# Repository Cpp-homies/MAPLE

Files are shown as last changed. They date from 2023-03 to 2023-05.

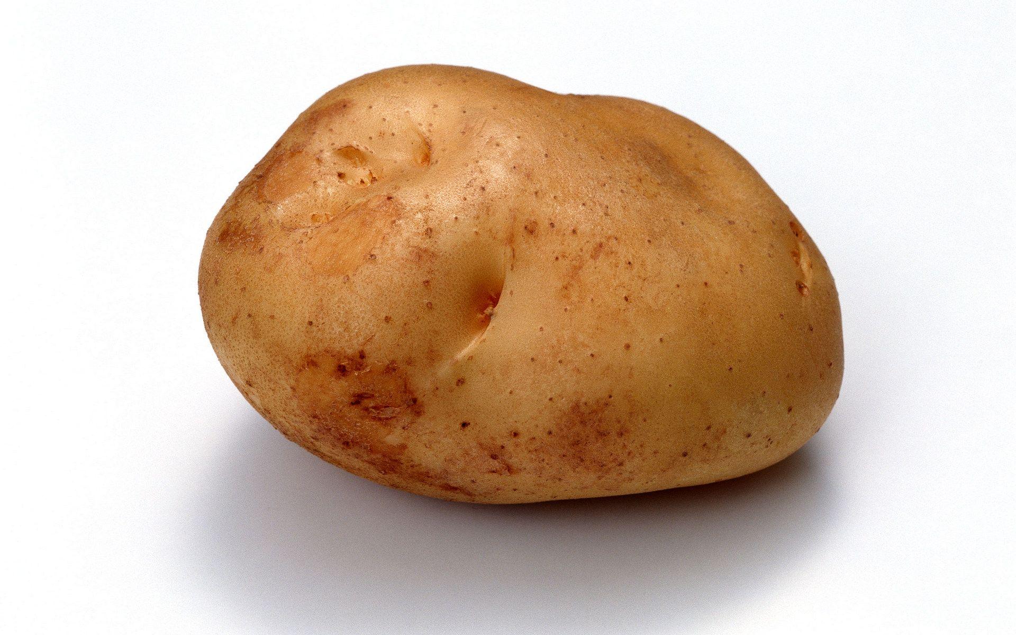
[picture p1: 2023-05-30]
Cloud/images_/potato.jpeg

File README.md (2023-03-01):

# M.A.P.L.E: Modular Automated Plant Life Enclosure

## Introduction to the project
Welcome to the public repository for our Design Thinking and Advanced Prototyping (ELEC-C9821) project, completed during the spring of 2023. Here, you can track the progress of our product development and review the process we followed to arrive at our final solution.

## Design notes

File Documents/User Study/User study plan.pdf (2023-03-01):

# User study plan - Team 3

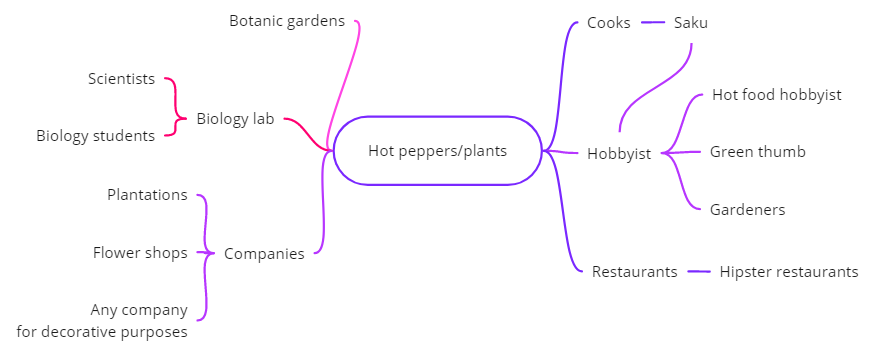
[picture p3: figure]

## 1. Target users

Since the trackable resource that we are interested in is plants, we have chosen hobbyists and enthusiasts as our target users, as they are potentially in need of plant-care automation. These users are also directly related to the resource (plants/hot peppers) since they are likely to have plants under their care.

This user group is quite accessible, as they could theoretically be anyone. For instance, we can reach out to other students in Aalto or other Universities and ask them to participate in our user study.

## 2. Methods

We have chosen to use multiple methods. To get a general understanding of peoples’ needs, we are conducting online surveys that are shared in facebook groups and also forwarded to enthusiasts and students by friends and family. The surveys are accessible through these links:

1. (Finnish)

https://docs.google.com/forms/d/e/1FAIpQLSeV6fbw9r-klXWt46JdWvNCtC_DFmbpAS877YtbKPnmx8KQeA/viewform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 (https://docs.google.com/forms/d/e/1FAIpQLSeV6fbw9r-klXWt46JdWvNCtC_DFmbpAS877YtbKPnmx8KQeA/viewform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)

2. (English)
https://docs.google.com/forms/d/e/1FAIpQLSdVMB6B2ZC3AZEyyUIAWT1qNiN2gCB68X5xvfQQSQ_5HiJimA/viewform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 (https://docs.google.com/forms/d/e/1FAIpQLSdVMB6B2ZC3AZEyyUIAWT1qNiN2gCB68X5xvfQQSQ_5HiJimA/viewform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)

Other methods of user studies will involve in-person or remote interviews mixed with co-design and design probing methods, if possible. That would give us a more personal view to the daily activities of enthusiasts and would open up the possibility for future user testing. (The first interview has already been arranged)

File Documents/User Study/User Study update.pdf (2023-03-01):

# User Study Update - Team 3

## 1. Target users

Our target users are plant hobbyists and enthusiasts. They are much more inclined to monitor their plants to a higher degree, and thus would be interested in a device to automate the monitoring of their plants to some extent.

This user group is quite accessible, as they could theoretically be anyone. For instance, we can reach out to other students in Aalto or other Universities and ask them to participate in our user study.

## 2. Current situation

We have already gotten 39 rather thorough responses with the online surveys that have given us a good insight into what people might be looking for in an IoT device meant for plant cultivation. In addition, the first interview has already been conducted and documented. It was a group interview with 2 potential users and was really informative. We believe the fact that 2 users could bounce ideas off of each other made it much more informative for us than it would have been otherwise.
Since we have already gathered enough information, we have started to map out the features and components of the device to slowly narrow down the idea.

Link to survey responses (english version): https://docs.google.com/spreadsheets/d/17iAOfix5XNTlHRVkv8-SSzz-9DiBaFzHnPxrE1_Iep0/edit?usp=sharing (https://docs.google.com/spreadsheets/d/17iAOfix5XNTlHRVkv8-SSzz-9DiBaFzHnPxrE1_Iep0/edit?usp=sharing)
Link to survey responses (finnish version): https://docs.google.com/spreadsheets/d/10vmuCnAydOV0NJCwSoHKujVEs_3GuGNUji77kcqlbv0/edit?usp=sharing (https://docs.google.com/spreadsheets/d/10vmuCnAydOV0NJCwSoHKujVEs_3GuGNUji77kcqlbv0/edit?usp=sharing)
Link to first interview notes: https://docs.google.com/document/d/13SDdg8U_1lrDhgf8Mg7o01ts4Be4uMcnlehz204QAec/edit?usp=sharing (https://docs.google.com/document/d/13SDdg8U_1lrDhgf8Mg7o01ts4Be4uMcnlehz204QAec/edit?usp=sharing)
Link to team Miro board:
https://miro.com/app/board/uXjVPy4PPEA=/?share_link_id=984503807965

## 3. User study methods

We have chosen to use multiple methods. To get a general understanding of people’s needs, we are conducting online surveys that are shared in facebook groups and also forwarded to enthusiasts and students by friends and family.

Other methods of user studies will involve in-person or remote interviews mixed with co-design and design probing methods, if possible. That would give us a more personal view of the daily activities of enthusiasts and would open up the possibility for future user testing.

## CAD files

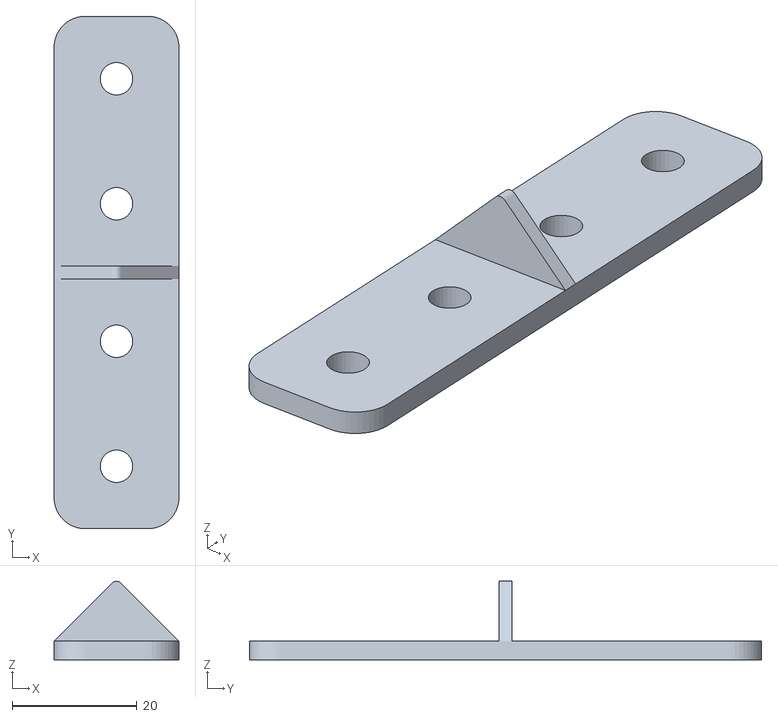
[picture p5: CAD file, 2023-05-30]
Physical/Frame/VerticalJoint.stl
20.0 x 82.0 x 12.6

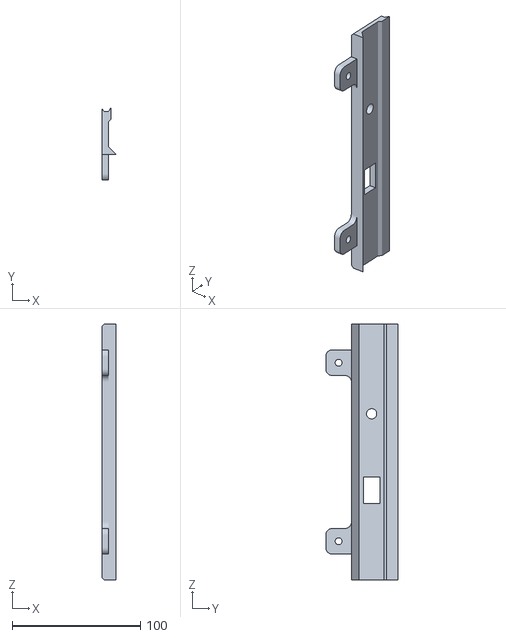
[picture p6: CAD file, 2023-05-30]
Physical/Panel/PanelHolder-Power v1.stl
11.2 x 56.5 x 199.6

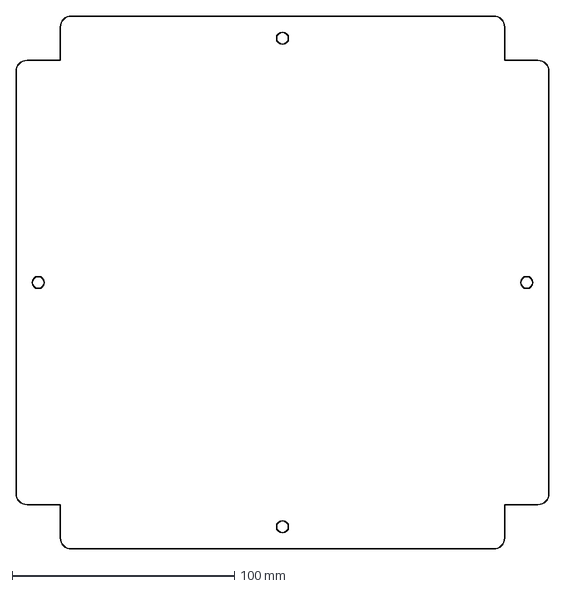
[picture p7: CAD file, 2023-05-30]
Physical/Plates/TopPanel v2.dxf
240.0 x 240.0 mm

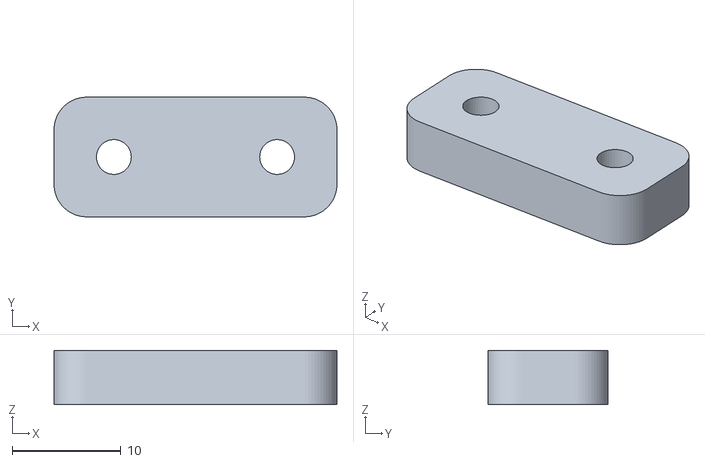
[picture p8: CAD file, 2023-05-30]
Physical/Pump/EndClamp v1.stl
26.0 x 11.0 x 5.00

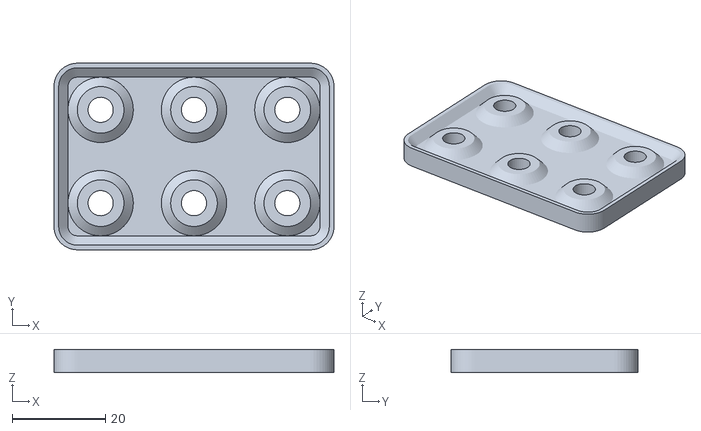
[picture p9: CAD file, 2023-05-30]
Physical/Frame/TBaseJoint v1.stl
60.0 x 40.0 x 5.00

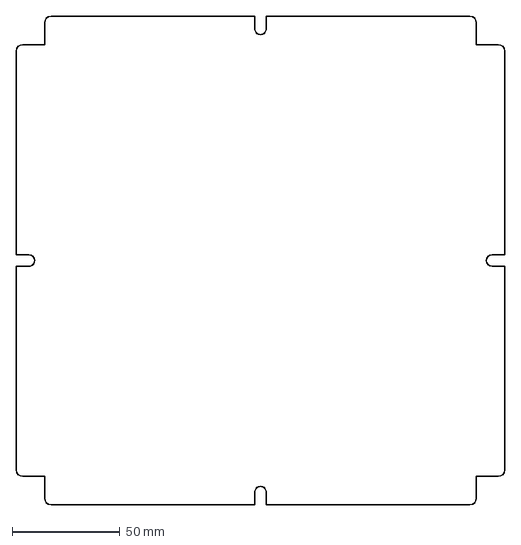
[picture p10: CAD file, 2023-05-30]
Physical/Plates/BottomPanel v1.dxf
226.0 x 226.0 mm

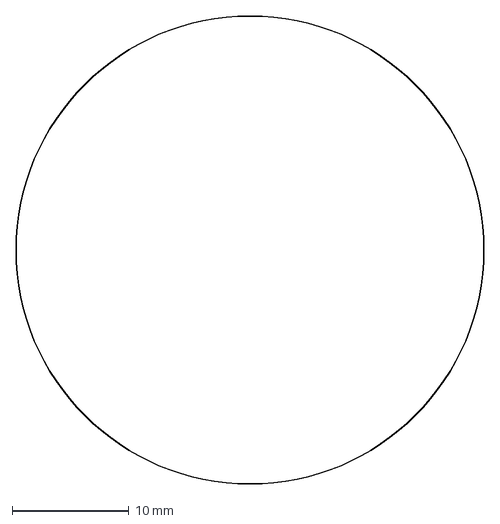
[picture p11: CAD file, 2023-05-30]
Physical/Plates/FanHole.dxf
40.0 x 40.0 mm

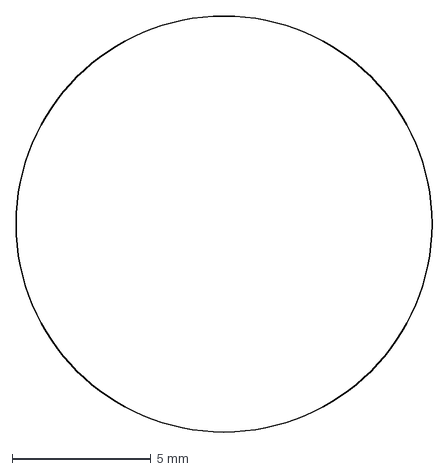
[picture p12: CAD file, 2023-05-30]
Physical/Plates/CableHole.dxf
15.0 x 15.0 mm

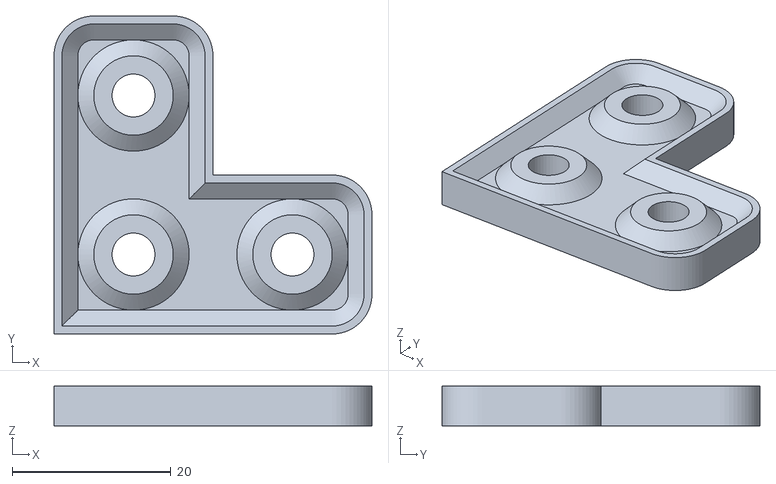
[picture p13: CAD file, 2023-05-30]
Physical/Frame/CornerJoint v2.stl
40.0 x 40.0 x 5.00

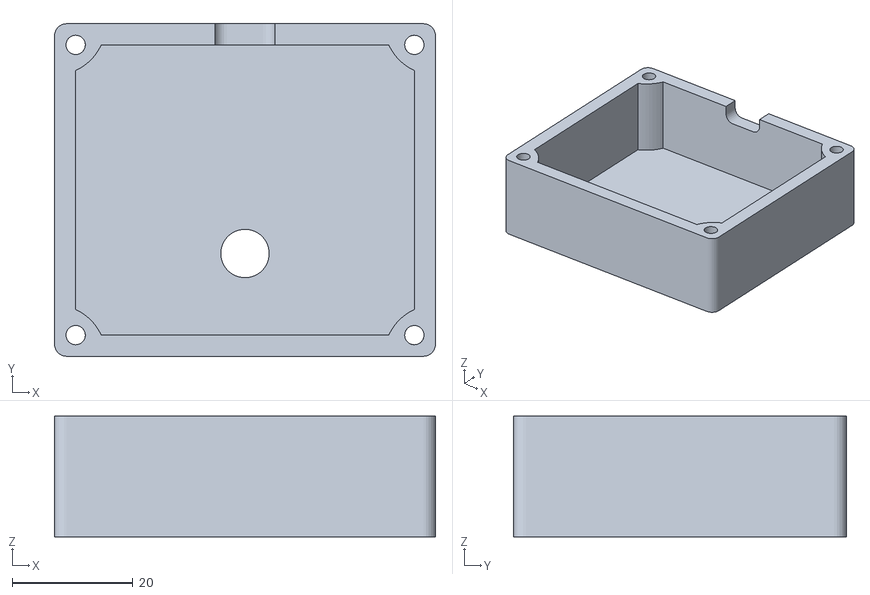
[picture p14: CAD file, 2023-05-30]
Physical/Mounts/ControlHolderC v2.stl
63.0 x 55.0 x 20.0

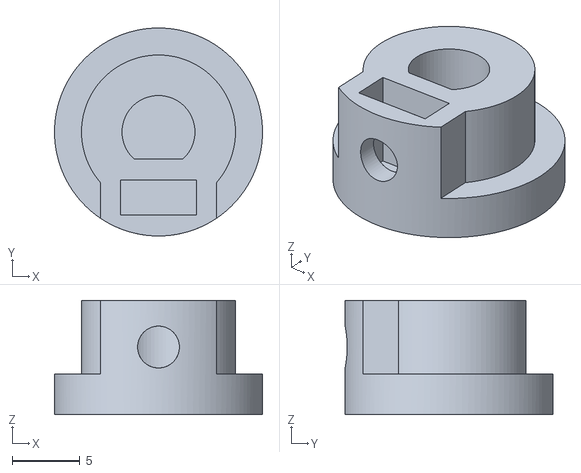
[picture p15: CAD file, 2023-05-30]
Physical/Pump/Stopper v2.stl
15.4 x 15.4 x 8.45

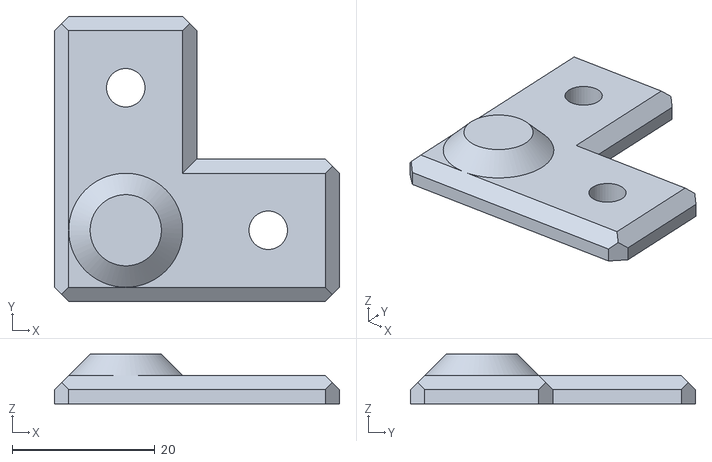
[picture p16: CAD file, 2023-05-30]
Physical/Frame/Feet v2.stl
40.0 x 40.0 x 7.00

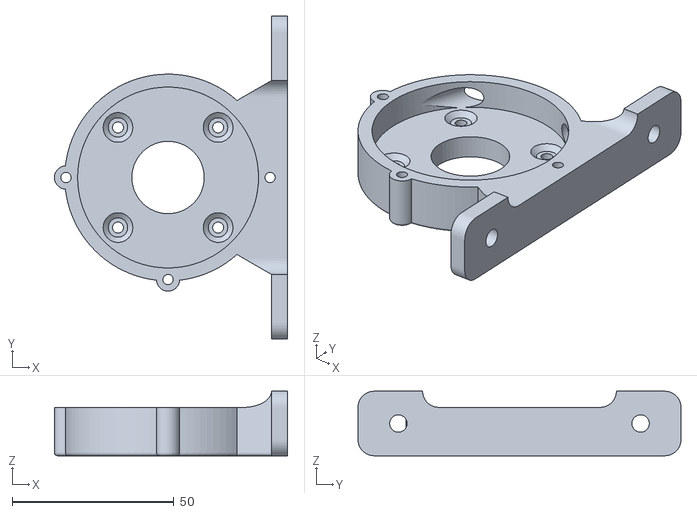
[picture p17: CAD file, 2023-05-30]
Physical/Pump/Pump v5.stl
72.2 x 100.0 x 20.0

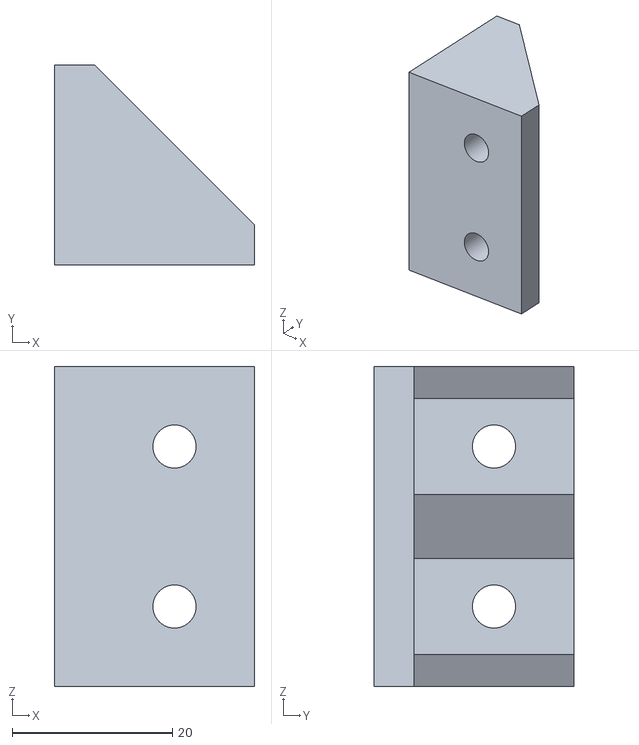
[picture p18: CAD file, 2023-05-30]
Physical/Frame/InternalJoint40 v1.stl
25.0 x 25.0 x 40.0

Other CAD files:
Physical/Panel/PanelHolder-Tube v1.stl
Physical/Mounts/ControllerBox v2.stl
Physical/Panel/Gripper v1.stl
Physical/Frame/CornerJoint.stl
Physical/Frame/CableCorner v1.stl
Physical/Frame/CableCorner v2.stl
Physical/Frame/CornerJointB v1.stl
Physical/Frame/Feet v1.stl
Physical/Frame/InternalJoint20 v1.stl
Physical/Frame/TTopJoint v1.stl
Physical/Frame/VerticalJoint v2.stl
Physical/Frame/VerticalJoint v3.stl
Physical/Frame/VerticalJoint v4.stl
Physical/Mounts/CableHolder v1.stl
Physical/Mounts/CableHolder v2.stl
Physical/Mounts/CableHolder v3.stl
Physical/Mounts/CableHolder-Flat v1.stl
Physical/Mounts/CableHolder-Flat v2.stl
Physical/Mounts/CameraMount v1.stl
Physical/Mounts/CameraMount v2.stl
Physical/Mounts/CameraMount v3.stl
Physical/Mounts/CameraMountB v1.stl
Physical/Mounts/CameraMountB v2.stl
Physical/Mounts/ConnectorMount v1.stl
Physical/Mounts/ConnectorMountL v1.stl
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

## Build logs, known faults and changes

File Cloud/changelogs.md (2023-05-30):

## Change logs
### — Recent changes —
### 24/05
**App to Cloud interaction**

- Data in a given time range can be requested through "/get-range/\<string:user_id\>/\<string:timerange\>"
    The format of the timerange is "%Y_%m_%d_%H_%M_%S-%Y_%m_%d_%H_%M_%S", or in other words, two time instances with start and end separated by the hyphen '-' character. 

    It is also possible to use the shorthand 'now' in place of the end time, which will result in a string with the form "%Y_%m_%d_%H_%M_%S-now". This will query data from the start time until the current time.
    
### 05/05
**App to Cloud interaction**  

- New method for deleting all data rows associated with a user was added. After authentication this can be accessed at "\<baseurl\>/delete-all/\<string:user_id\>"

### — Archived changes — 
### 11/04
**Device to Cloud interaction**

- The "\<baseurl\>/request-to-esp/\<user_id:string\>" is now moved to "\<baseurl\>/request-to-esp/\<user_id:string\>/\<password:string\>"
- A new URL was made specifically for PUT request from the ESP, at "\<baseurl\>/esp-req/sensordata/&lt;string:timestamp&gt;" with the "user_id" and "password" being added to the arguments

### 07/04
**App to Cloud interaction**

- A new user_id and password hash pair can be add to the database by sending PUT to "\<base url\>/auth/register" with two parameters "user_id" and "password"
- A hashed user_id and password pair can be check by sending GET to "\<base url\>/auth/login" with two parameters "user_id" and "password". This will have the following return values
	- 404 HTTP response code: username not found
	- a dictionary with "status" attributes:
		- `response["status"] == 0`: password does not match the one in the database, authentication failed
		- `response["status"] == 1`: password matches the one in the database, authentication was successful
- User's password can be change using PATCH requets to "\<base url\>/auth/login" with two parameters "user_id" and "password".
- A session must be authenticate by logging in first before any request can be made.
- 

### 05/04
**App to Cloud interaction**

- For PUT and UPDATE request: added soil humidity "soil_humid", the old "humid" key in the json will be change to "air_humid"
- For GET request: added soil humidity "soil_humidity", and change the old "humid" key into "air_humidity"
- Sensor data resource now located at "\<base url\>/sensordata/\<string:user_id\>/\<string:timestamp\>" instead of "\<base url\>/sensordata/\<string:timestamp\>/" in order to distinguish data entries from different users and their devices. All requests that previously went to the mentioned URL should now be redirected to the new one.
- The "\<baseurl\>/datatable" resource is now moved to "\<baseurl\>/datatable/\<user_id:string\>" to distinguish between the users. All requests that previously went to the mentioned URL should now be redirected to the new one.

**Device to Cloud interaction**

- The "\<baseurl\>/datatable" resource is now moved to "\<baseurl\>/datatable/\<user_id:string\>" to distinguish between the users
- The "\<baseurl\>/request-to-esp" resource is now moved to "\<baseurl\>/request-to-esp/\<user_id:string\>" to distinguish between the users. All requests that previously went to the mentioned URL should now be redirected to the new one.

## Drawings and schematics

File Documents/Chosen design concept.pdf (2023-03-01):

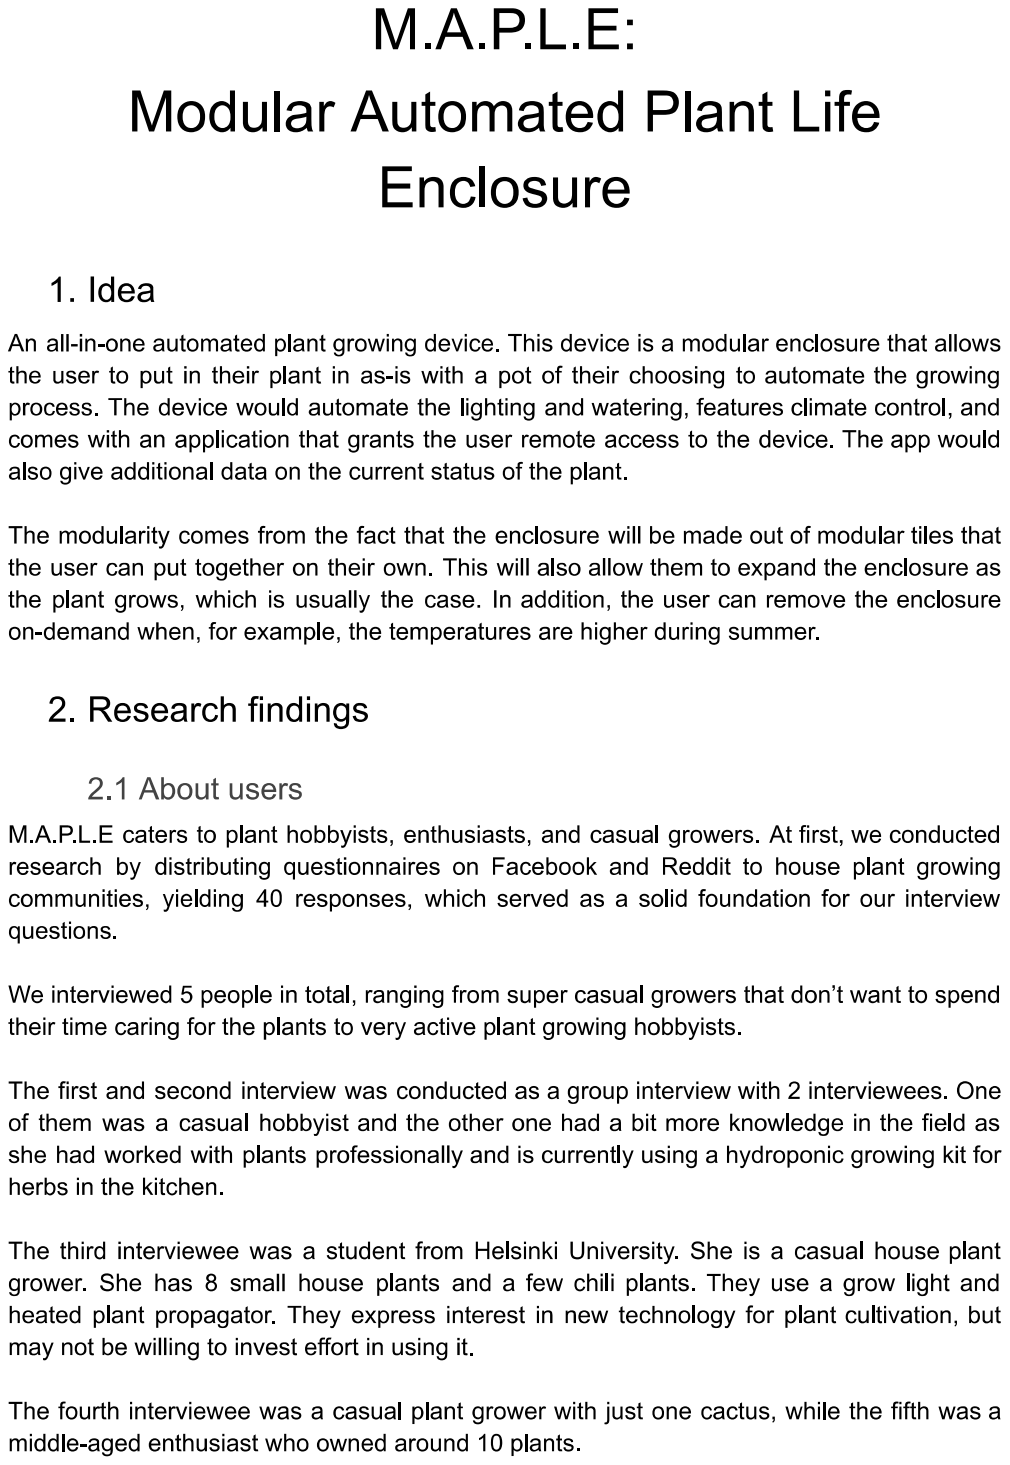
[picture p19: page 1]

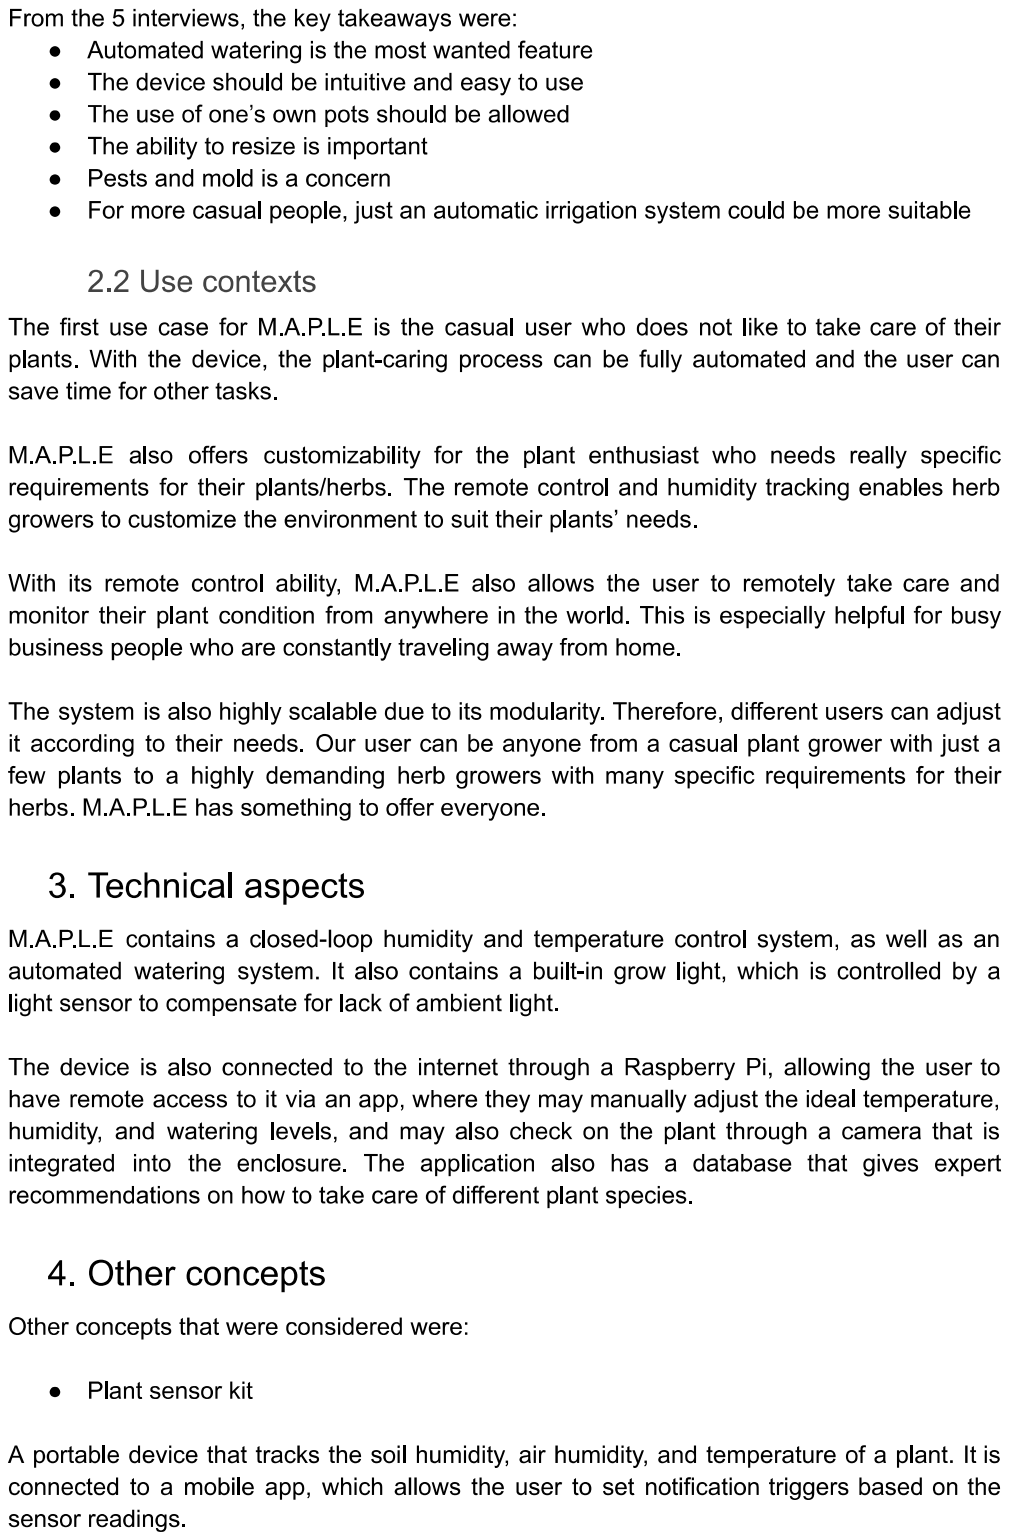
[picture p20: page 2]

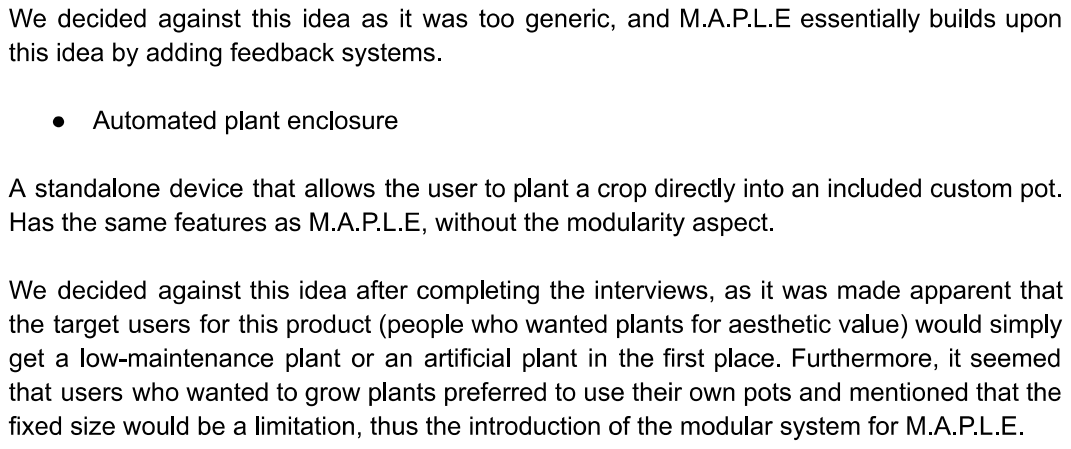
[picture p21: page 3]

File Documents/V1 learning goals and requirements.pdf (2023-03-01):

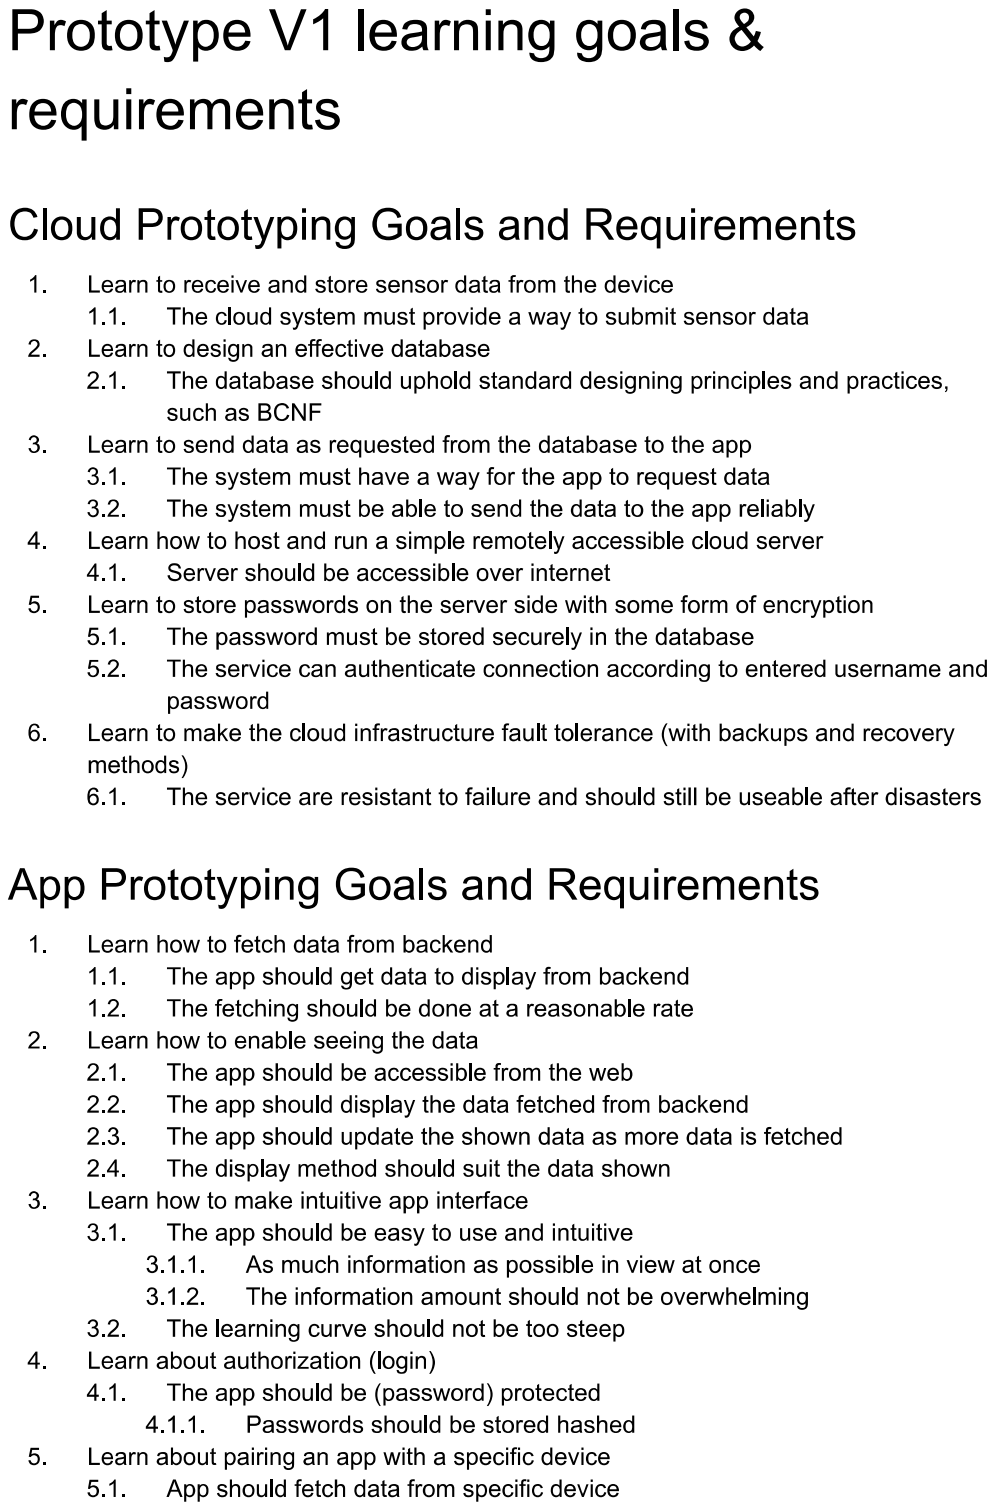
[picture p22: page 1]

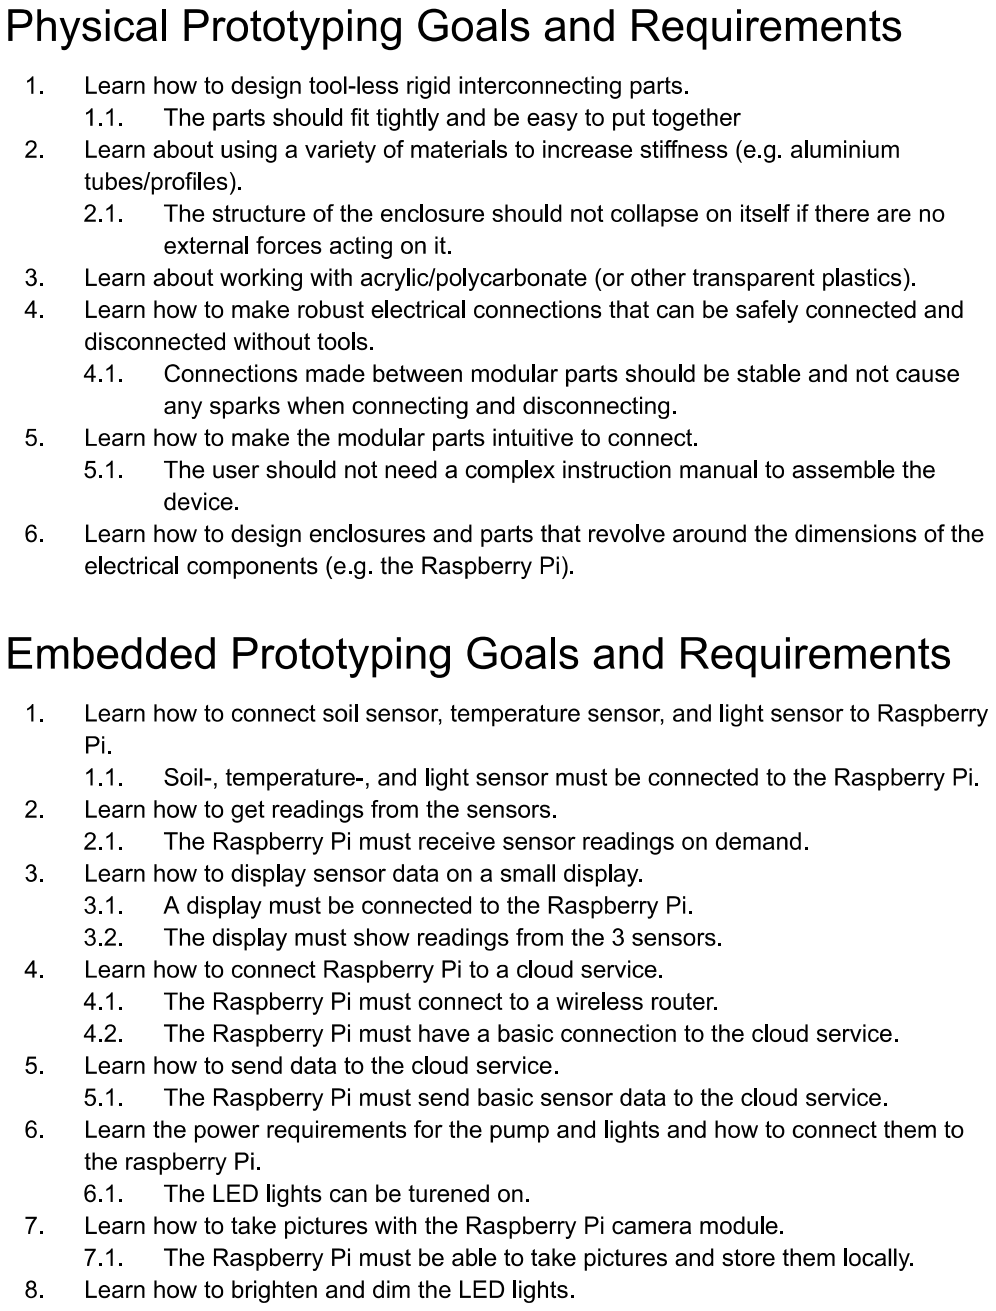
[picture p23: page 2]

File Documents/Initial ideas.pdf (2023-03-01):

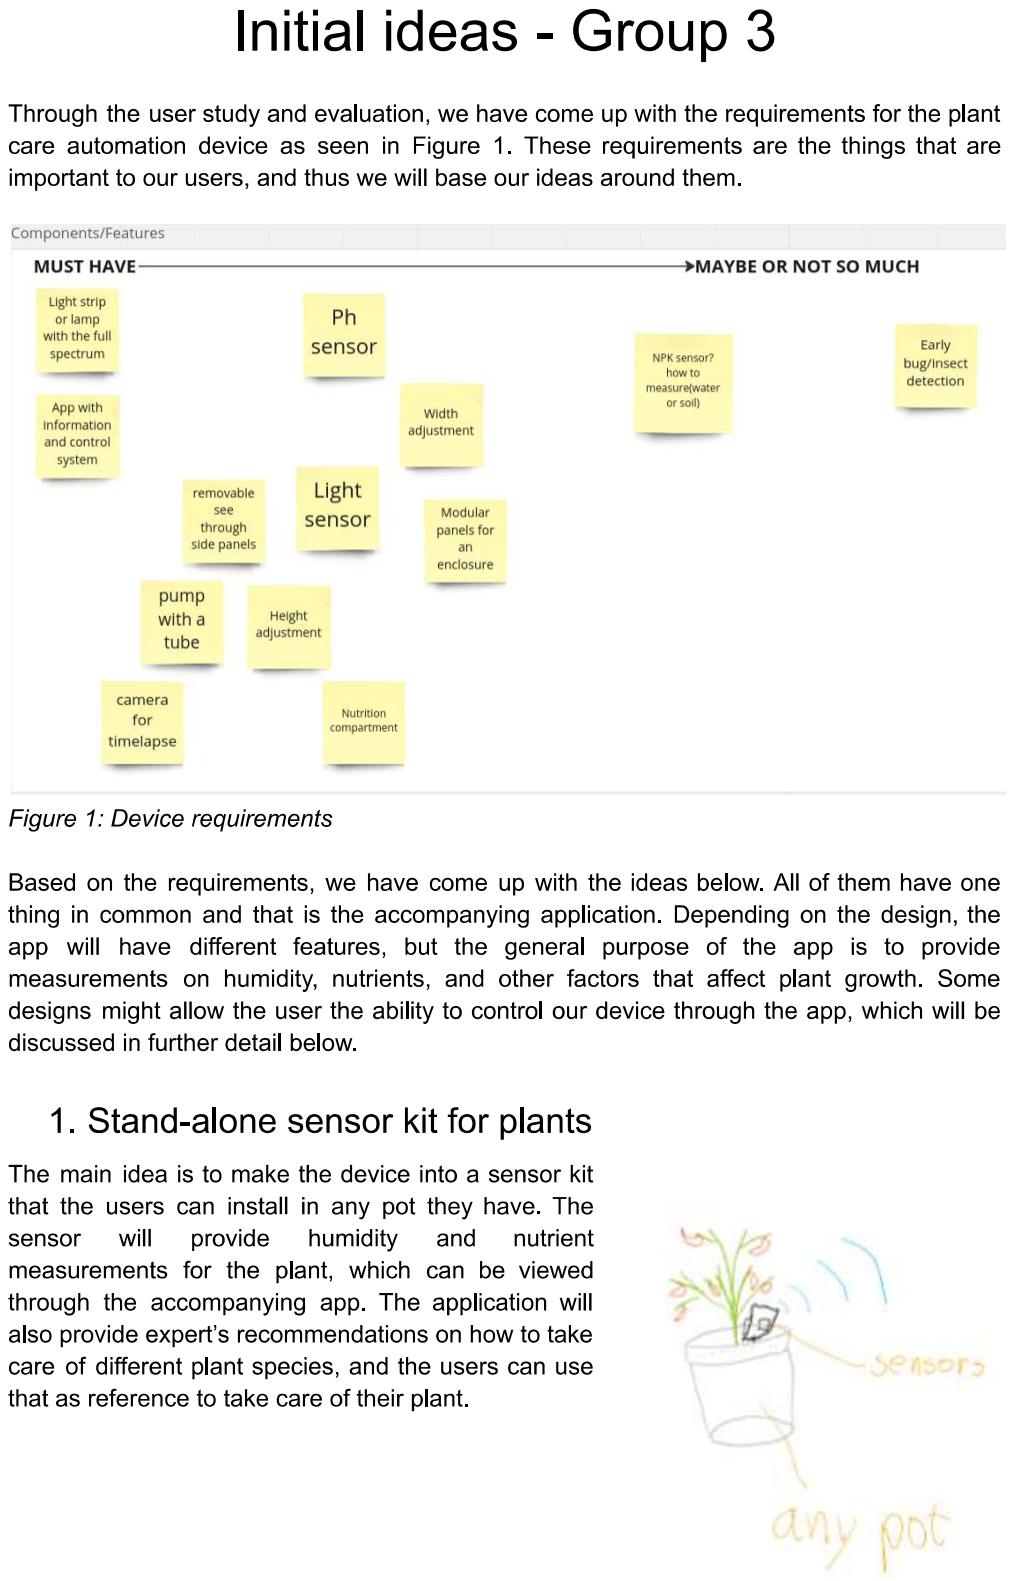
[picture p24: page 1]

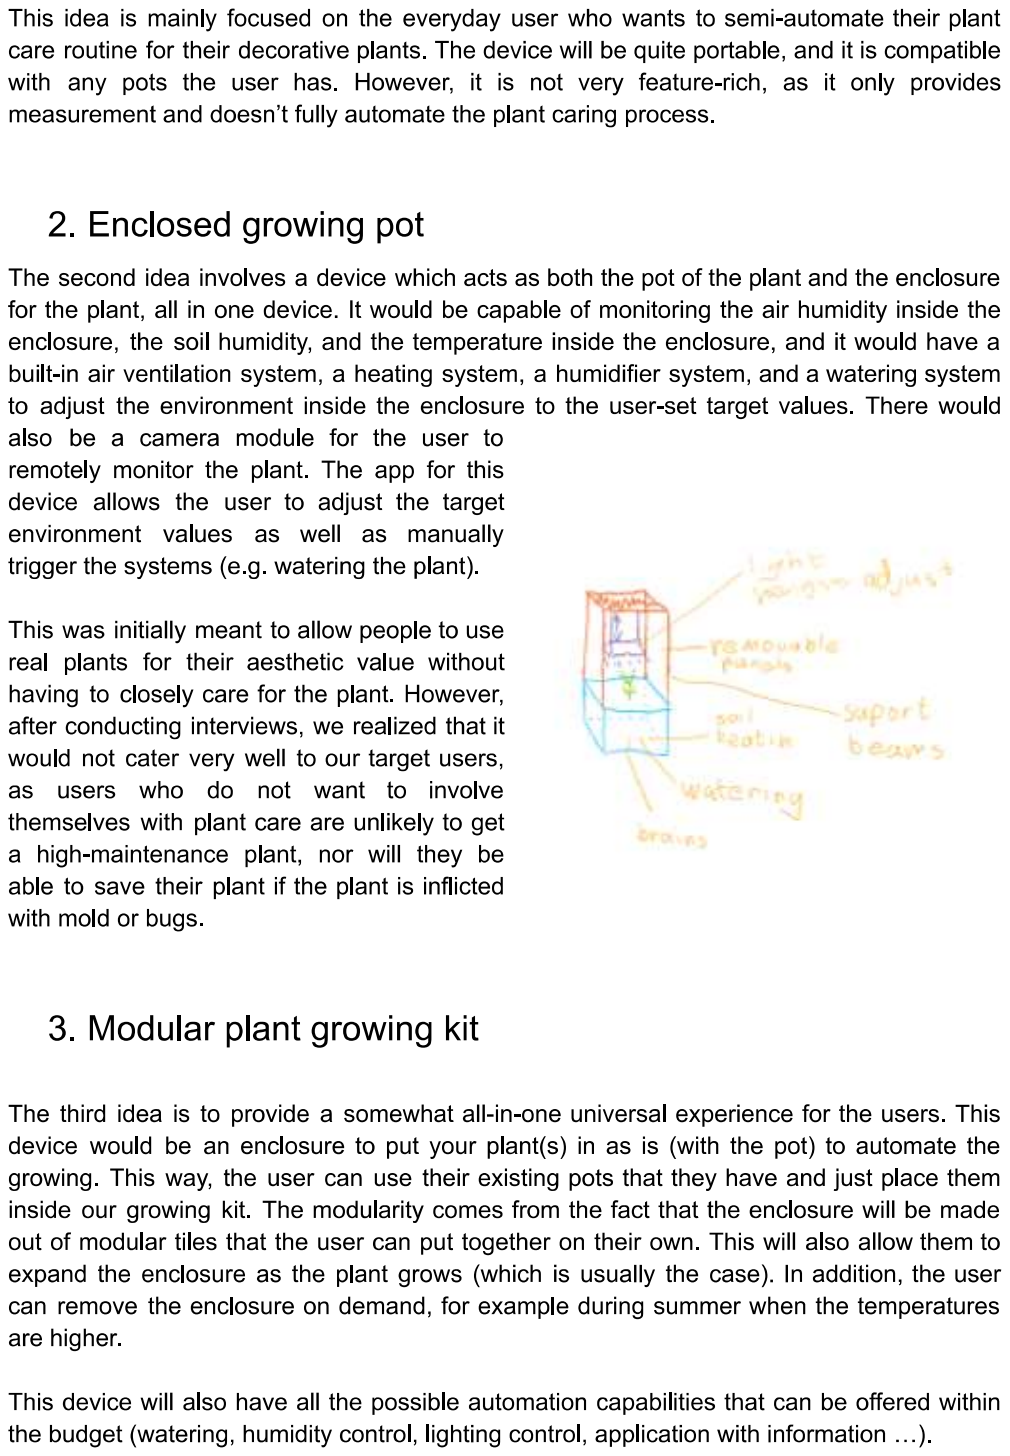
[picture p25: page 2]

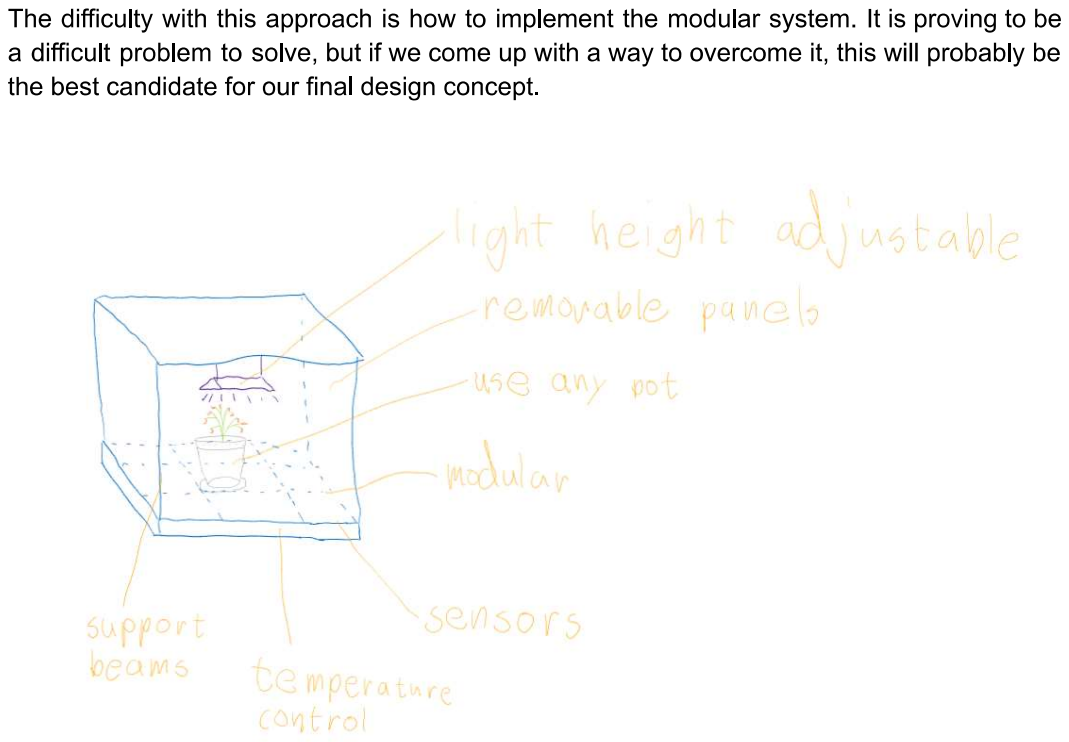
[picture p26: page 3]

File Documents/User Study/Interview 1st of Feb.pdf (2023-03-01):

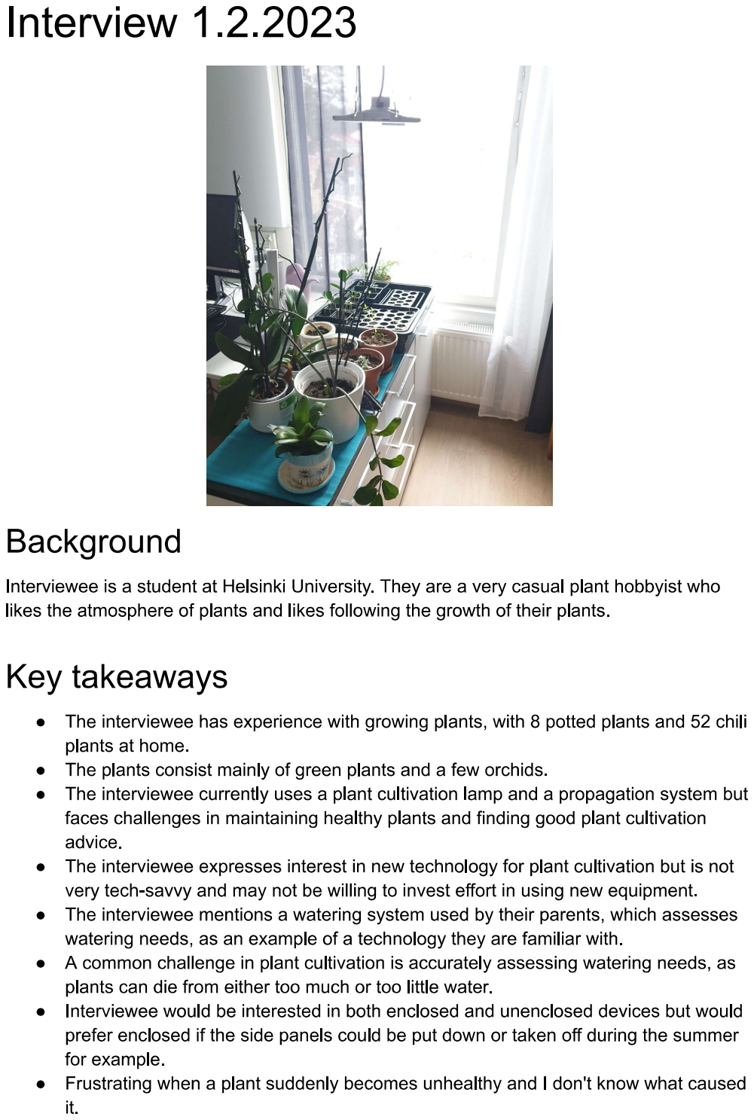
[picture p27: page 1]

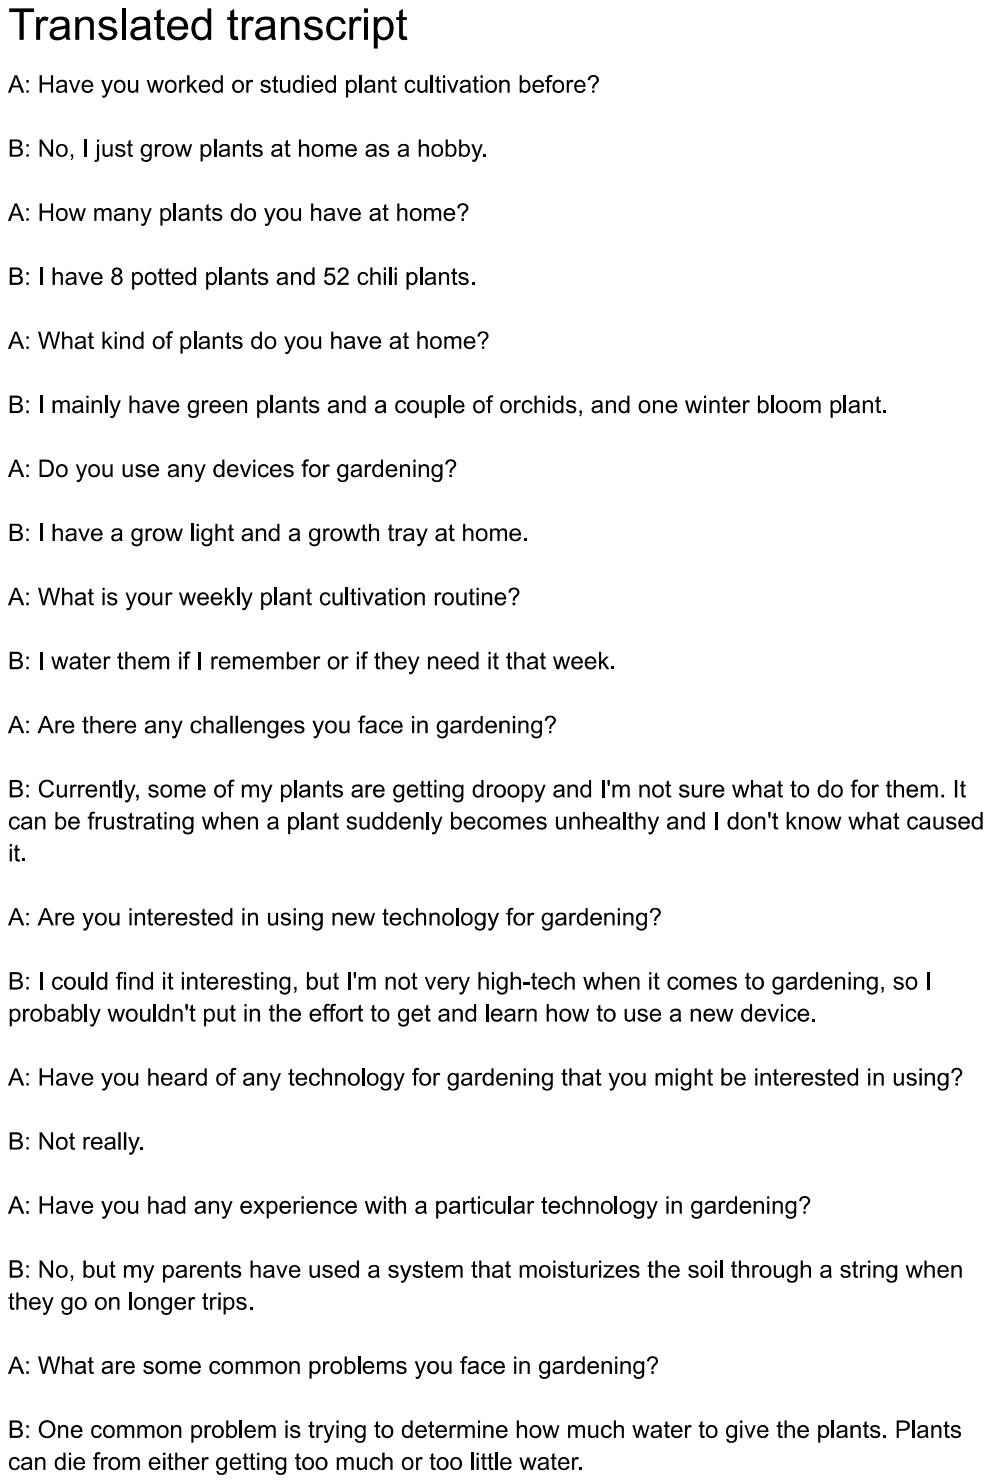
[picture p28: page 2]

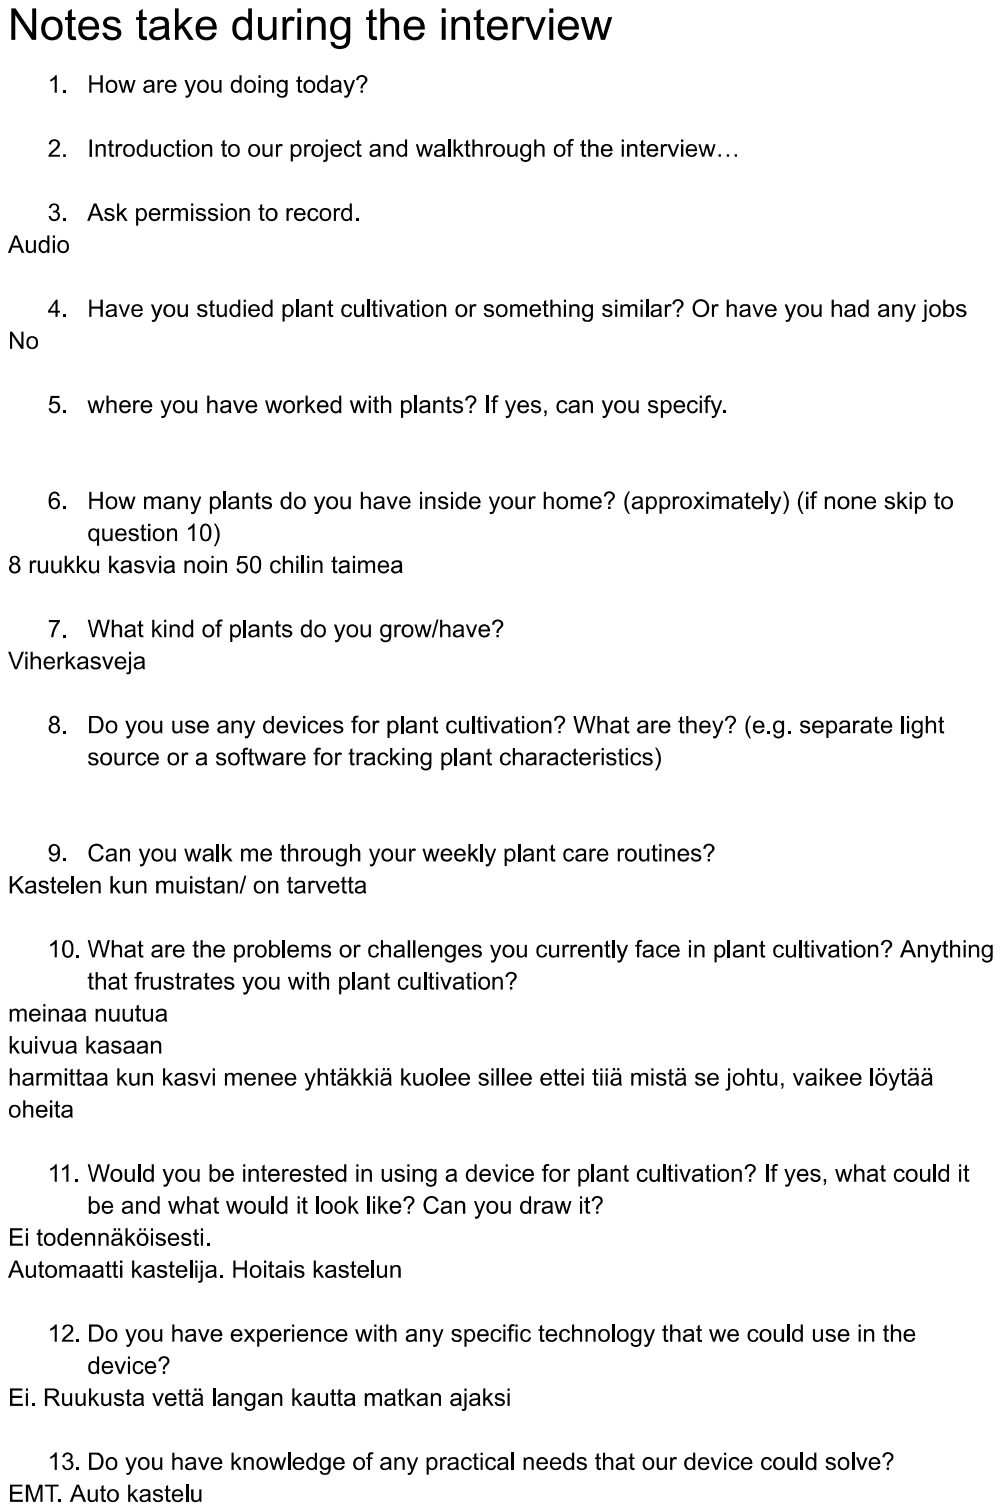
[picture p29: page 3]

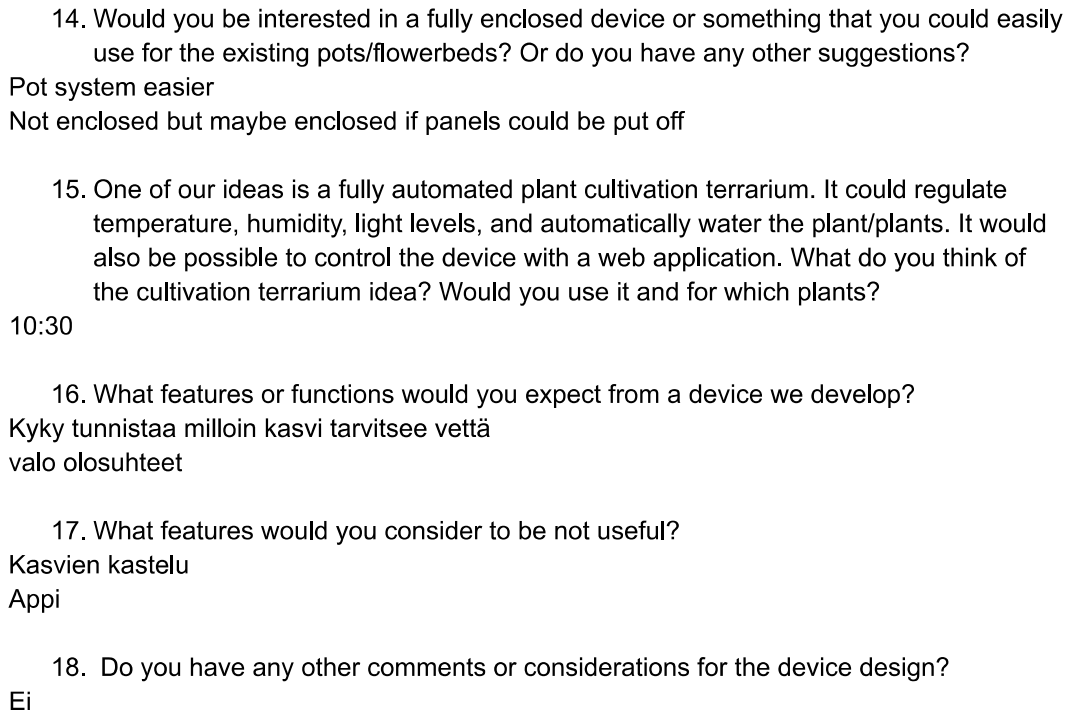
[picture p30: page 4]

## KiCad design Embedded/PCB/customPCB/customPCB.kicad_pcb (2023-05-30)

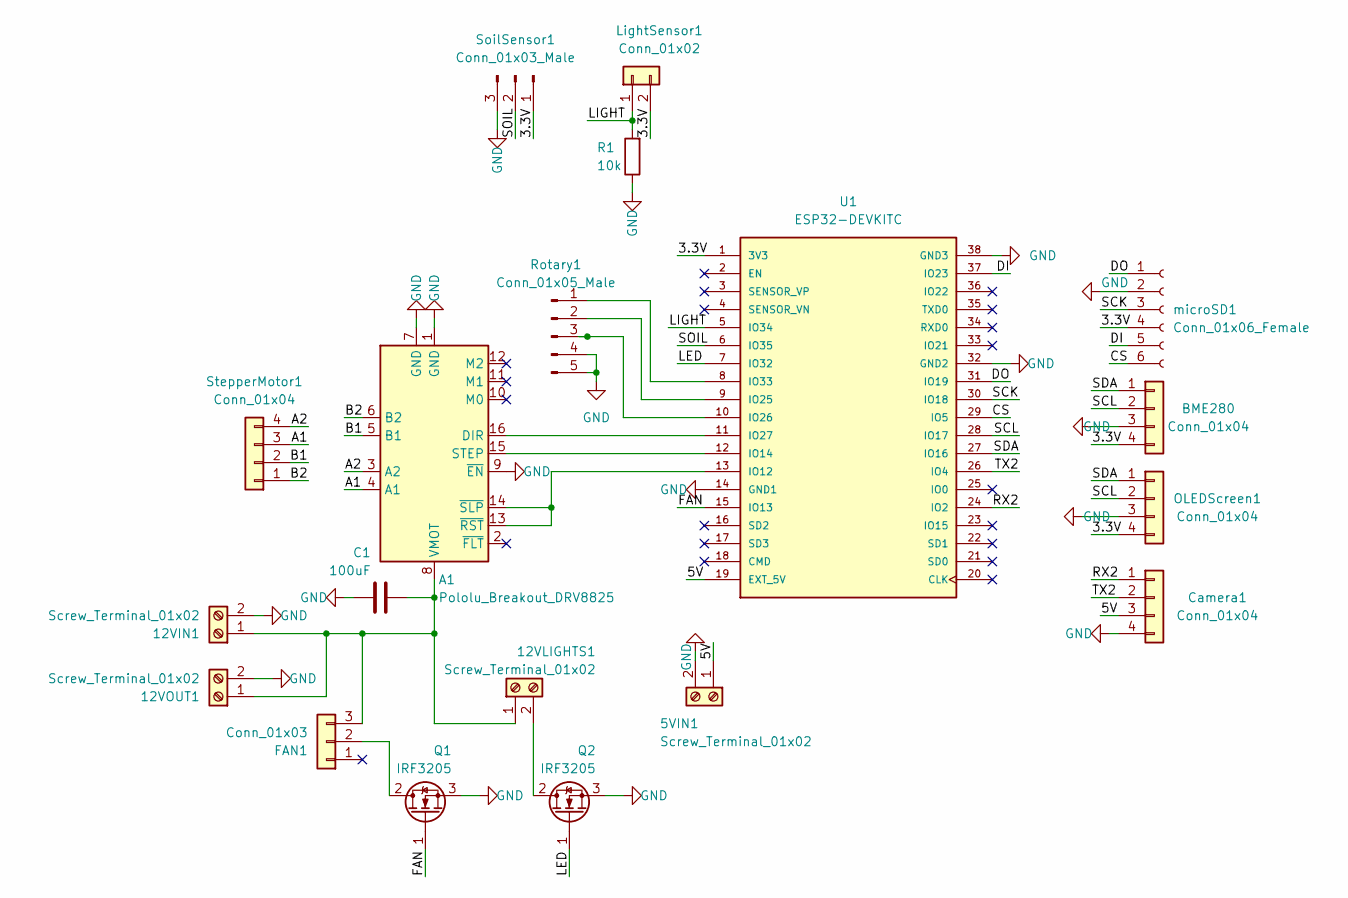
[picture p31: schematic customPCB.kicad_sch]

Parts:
5VIN1, 12VIN1, 12VLIGHTS1, 12VOUT1: Screw_Terminal_01x02; 691502710002
A1: Pololu_Breakout_DRV8825; Pololu_Breakout-16_15.2x20.3mm
BME280: Conn_01x04; JST_XH_B4B-XH-A_1x04_P2.50mm_Vertical
C1: 100uF; C_0805_2012Metric
Camera1: Conn_01x04; JST_XH_B4B-XH-A_1x04_P2.50mm_Vertical
FAN1: Conn_01x03; JST_XH_B3B-XH-A_1x03_P2.50mm_Vertical
LightSensor1: Conn_01x02; JST_XH_B2B-XH-A_1x02_P2.50mm_Vertical
OLEDScreen1: Conn_01x04; JST_XH_B4B-XH-A_1x04_P2.50mm_Vertical
Q1, Q2: IRF3205; TO254P1524X483-4N
R1: 10k; R_0805_2012Metric
Rotary1: Conn_01x05_Male; PinHeader_1x05_P2.54mm_Vertical
SoilSensor1: Conn_01x03_Male; PinHeader_1x03_P2.54mm_Vertical
StepperMotor1: Conn_01x04; JST_XH_B4B-XH-A_1x04_P2.50mm_Vertical
U1: ESP32-DEVKITC; MODULE_ESP32-DEVKITC; PARTREV N/A
microSD1: Conn_01x06_Female; PinSocket_1x06_P2.54mm_Vertical

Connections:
/3.3V: BME280.4, LightSensor1.2, OLEDScreen1.4, SoilSensor1.1, U1.1 (3V3), microSD1.4
/5V: 5VIN1.1, Camera1.3, U1.19 (EXT_5V)
/A1: A1.4 (A1), StepperMotor1.3
/A2: A1.3 (A2), StepperMotor1.4
/B1: A1.5 (B1), StepperMotor1.2
/B2: A1.6 (B2), StepperMotor1.1
/CS: U1.29 (IO5), microSD1.6
/DI: U1.37 (IO23), microSD1.5
/DO: U1.31 (IO19), microSD1.1
/FAN: Q1.1 (G), U1.15 (IO13)
/LED: Q2.1 (G), U1.7 (IO32)
/LIGHT: LightSensor1.1, R1.2, U1.5 (IO34)
/RX2: Camera1.1, U1.24 (IO2)
/SCK: U1.30 (IO18), microSD1.3
/SCL: BME280.2, OLEDScreen1.2, U1.28 (IO17)
/SDA: BME280.1, OLEDScreen1.1, U1.27 (IO16)
/SOIL: SoilSensor1.2, U1.6 (IO35)
/TX2: Camera1.2, U1.26 (IO4)
GND: 5VIN1.2, 12VIN1.2, 12VOUT1.2, A1.1 (GND), A1.7 (GND), A1.9 (~EN), BME280.3, C1.1, Camera1.4, OLEDScreen1.3, Q1.3 (S), Q2.3 (S), R1.1, Rotary1.4, Rotary1.5, SoilSensor1.3, U1.14 (GND1), U1.32 (GND2), U1.38 (GND3), microSD1.2
unnamed: 12VIN1.1, 12VLIGHTS1.1, 12VOUT1.1, A1.8 (VMOT), C1.2, FAN1.3
unnamed: 12VLIGHTS1.2, Q2.2 (D)
unnamed: A1.13 (~RST), A1.14 (~SLP), U1.13 (IO12)
unnamed: A1.15 (STEP), U1.12 (IO14)
unnamed: A1.16 (DIR), U1.11 (IO27)
unnamed: FAN1.2, Q1.2 (D)
unnamed: Rotary1.1, U1.8 (IO33)
unnamed: Rotary1.2, U1.9 (IO25)
unnamed: Rotary1.3, U1.10 (IO26)

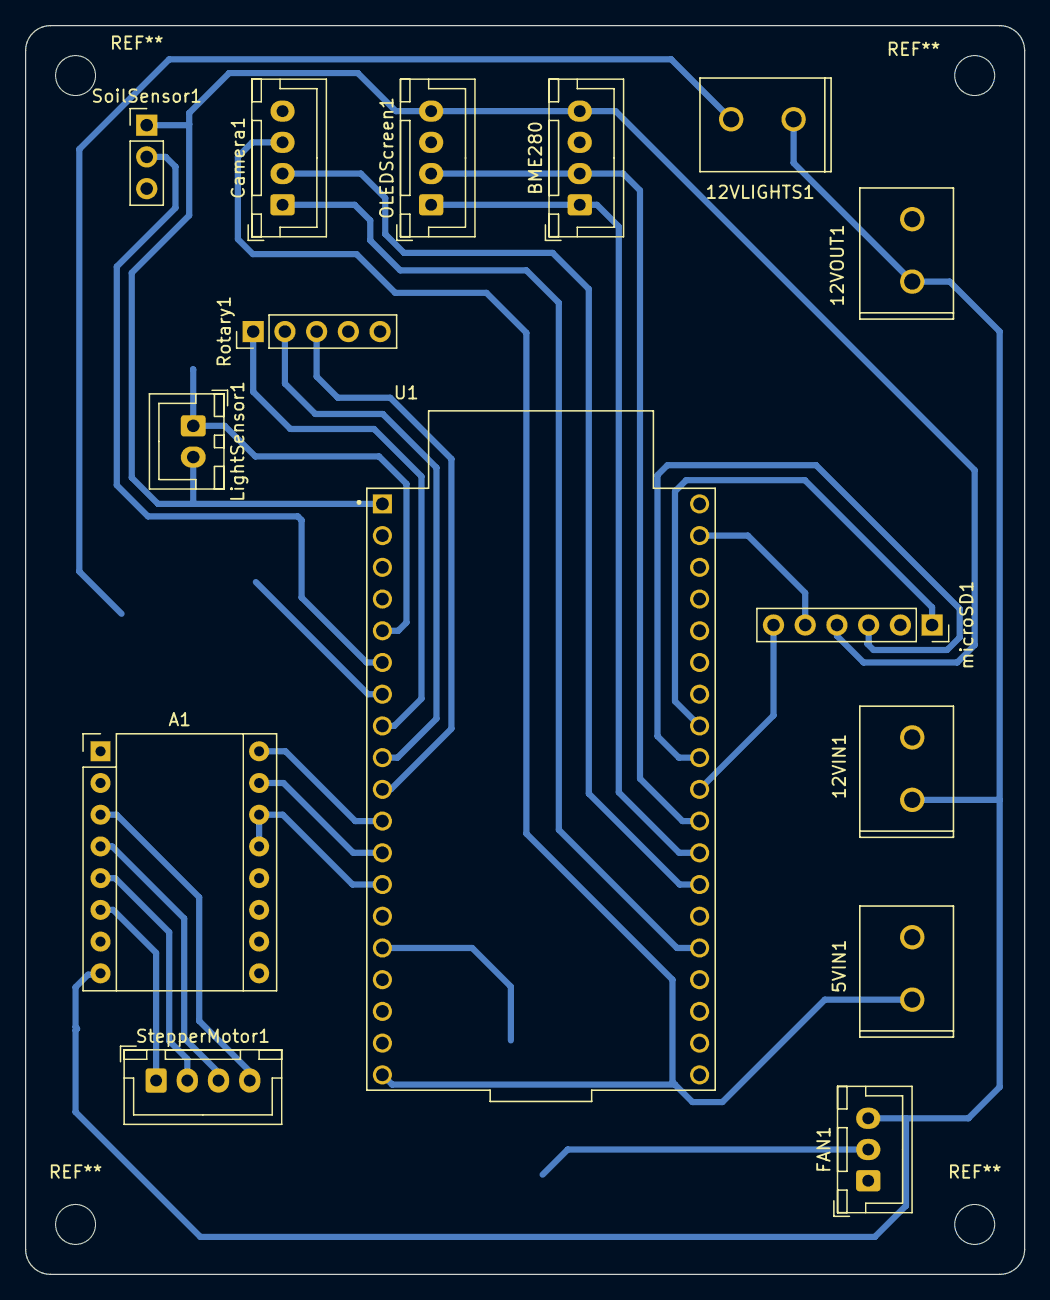
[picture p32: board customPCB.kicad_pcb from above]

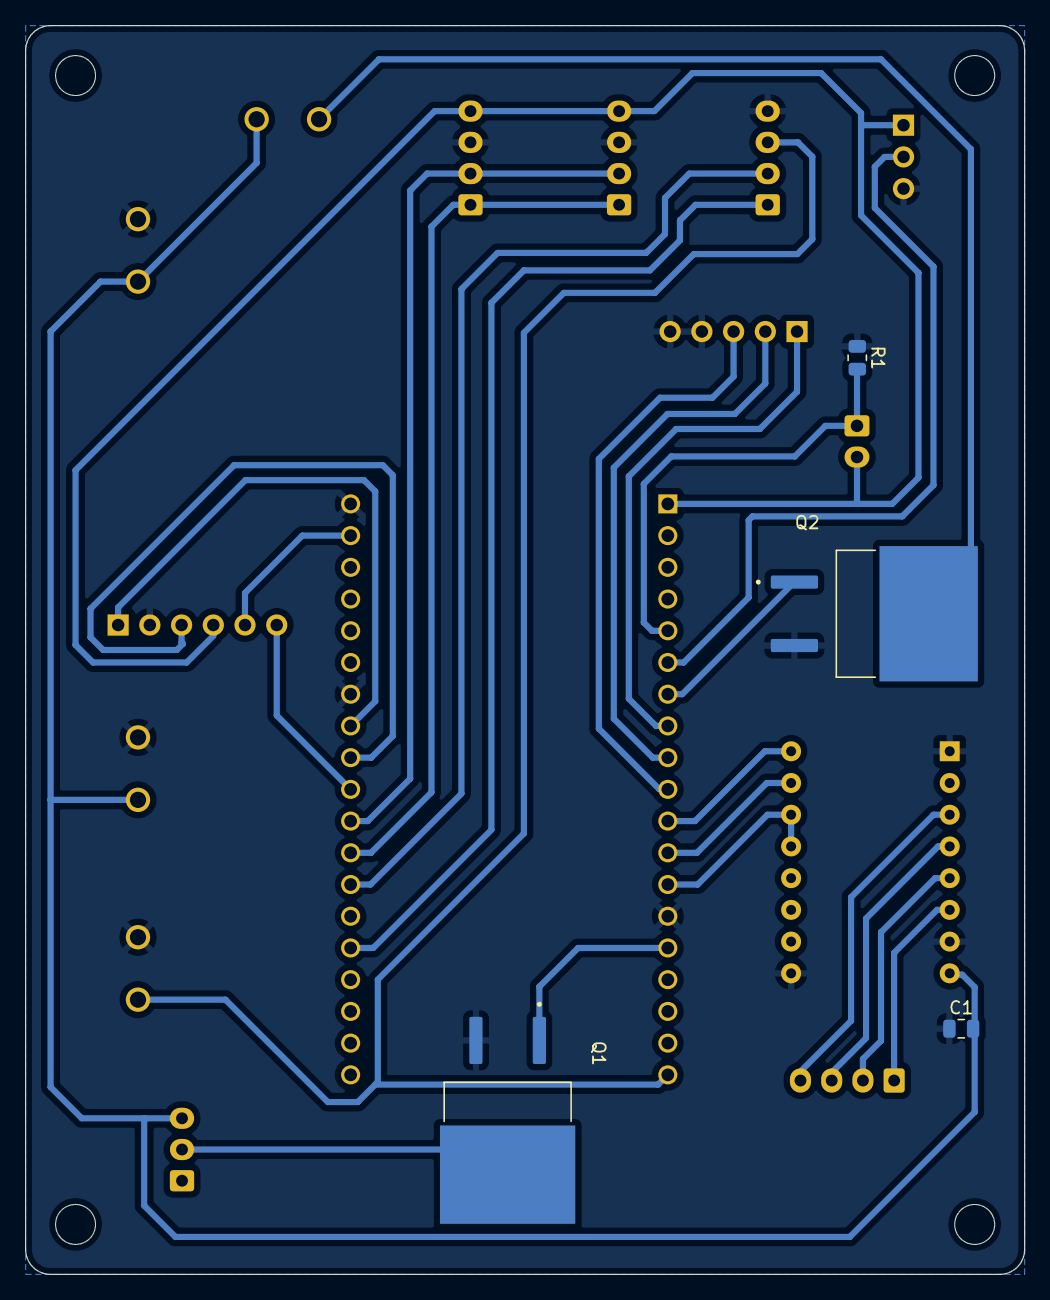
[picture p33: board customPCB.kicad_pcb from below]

Board: 2 copper layers, 80.0 x 100.0 mm, 19 parts (4 on the bottom side), 28 nets.

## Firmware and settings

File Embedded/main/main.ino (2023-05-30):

#include <Wire.h>
#include <Adafruit_GFX.h>
#include <Adafruit_SSD1306.h>
#include <Adafruit_Sensor.h>
#include <Adafruit_BME280.h>
#include "Button2.h" //  https://github.com/LennartHennigs
#include "ESPRotary.h" //  https://github.com/LennartHennigs
#include <WiFi.h>
#include "mbedtls/md.h"
#include <HTTPClient.h>
#include <ArduinoJson.h>
#include <time.h>
#include <string.h>
// File System Library
#include <FS.h>
// SPI Flash Syetem Library
#include <SPIFFS.h>
// WiFiManager Library
#include <WiFiManager.h>
#include "SD.h"
#include "SPI.h"
#include <HardwareSerial.h>
#include <AccelStepper.h>

//OLED
#define SCREEN_WIDTH 128 
#define SCREEN_HEIGHT 64 
//Wifi config
#define ESP_DRD_USE_SPIFFS true
#define JSON_CONFIG_FILE "/config_maple_user.json"
//rotary
#define CLICKS_PER_STEP   4
#define MIN_POS 0
#define MAX_POS 4
#define INCREMENT 1
//pump motor
#define motorInterfaceType 1
//GPIO pins
#define ROTARY_PIN1	33
#define ROTARY_PIN2	25
#define BUTTON_PIN	26
#define LIGHT_SENSOR 34
#define SOIL_SENSOR 35
//#define DIR 27
//#define STEP 14
#define LIGHTS 32
#define FAN 13
#define PUMP_POWER 12
#define RX_PORT2 2
#define TX_PORT2 4
#define I2C_SDA 16
#define I2C_SCL 17

const int STEP = 14;
const int DIR = 27;

//PWM variables
int freq = 2000;
int pwmResolution = 8;
int pwmChannel_0 = 0;
int pwmChannel_2 = 2;

int lightCheckPreviousMillis = 0;
int lightCheckInterval = 10000; 
int pumpCheckPreviousMillis = 0;
int pumpCheckInterval = 10000;
int pumpInterval = 10000; 
uint16_t analogWet = 1420;
uint16_t analogDry = 2950;
uint16_t lightCutOff = 90;
uint16_t lightMax = 10;
uint16_t pumpTriggerPercent = 30;
int pumpStopPercent = 85;
bool watering = false;
String pumpingTime = "N/A";
uint8_t brightness;
int lightPercentage = 100;
String lightStartTime = "08:00";
String lightStopTime = "22:00";
int pumpSpeed = 800;
int fanSpeed = 240; //190-255
int fanThreshold = 50;
bool fanOn = false;
uint8_t screenMode = 0; //to define what to show on screen
bool executeMenu = false;
bool inWifiConfig = false;
bool offlineMode = true;
uint8_t menuPosition = 0;
bool reset = false;
const char *dataFile = "/mapleData.csv"; //data logging file path
hw_timer_t *timer = NULL; //rotary timer
uint32_t I2Cfreq = 100000;


TwoWire I2C = TwoWire(0);
Adafruit_SSD1306 display(SCREEN_WIDTH, SCREEN_HEIGHT, &I2C, -1);
Adafruit_BME280 bme;
HardwareSerial SerialPort(2); //UART2
ESPRotary r;
Button2 b;
AccelStepper stepper(motorInterfaceType, STEP, DIR);

String myTimezone ="EET-2EEST,M3.5.0/3,M10.5.0/4";

unsigned long previousMillis = 0;
const long interval = 30000;
String BASE_URL = "https://cloud.kovanen.io/";
// String BASE_URL = "https://mapleplantapi.azurewebsites.net/";
// String BASE_URL = "http://10.0.0.6:8001/";
 
// Flag for saving config data
bool shouldSaveConfig = false;
 
// Variables to hold data from custom textboxes
char usernameString[50] = "Username";
char passwordString[50] = "Password";

// The hashedString and password
String hashedUsername;
String hashedPassword;

// The session cookies for one time authentication
// Extract the session cookie from the response headers
String sessionCookie;
 
// Define WiFiManager Object
WiFiManager wm;

/////////////////////////////////////////////
// Device-Cloud communication methods
TaskHandle_t listenerHandle;

// The HTTPClient object used for communication
// HTTPClient http;

// Function that get incoming request from the cloud
// return the HTTP response code, and change the JSON document requestArgs to contain any input arguments for the request (if any)
int getNewRequest(DynamicJsonDocument *requestArgs) {
    // Create the address
    String address = BASE_URL + "request-to-esp/" + hashedUsername + "/" + hashedPassword;
    HTTPClient http;
    http.begin(address);
    Serial.println("Sending request to " + address);
    // Send HTTP GET request to the cloud to check for incoming request
    // http.setCookie("session", session["auth_user"]);
    http.addHeader("session", sessionCookie);
    int httpResponseCode = http.GET();

    if (httpResponseCode > 0) {
        // Parse the response JSON
        String response = http.getString();
        DeserializationError error = deserializeJson(*requestArgs, response);
        if (error) {
            Serial.println("Failed to parse JSON response");
            return -1;
        }
        http.end();
        return httpResponseCode;
    } else {
        http.end();
        return httpResponseCode;
    }
}

// function for updating the control parameter on the cloud server
void updateCloudControlParameters(int lightPercentage, int fanThreshold, int pumpTriggerPercent, String lightStartTime, String lightStopTime) {
  // Create a JSON payload with the control parameters
  StaticJsonDocument<512> jsonPayload;
  jsonPayload["lightIntensity"] = lightPercentage;
  jsonPayload["fanThreshold"] = fanThreshold;
  jsonPayload["pumpThreshold"] = pumpTriggerPercent;
  jsonPayload["lightStartTime"] = lightStartTime;
  jsonPayload["lightStopTime"] = lightStopTime;
  jsonPayload["user_id"] = hashedUsername;
  jsonPayload["password"] = hashedPassword;

  // Serialize the JSON payload to a string
  String payloadString;
  serializeJson(jsonPayload, payloadString);

  String address = BASE_URL + "/esp-control-pars-update";
  HTTPClient http;
  http.begin(address);

  // Set the content type header to JSON
  http.addHeader("Content-Type", "application/json");

  // Send the PUT request with the JSON payload
  int httpResponseCode = http.PUT(payloadString);
  if (httpResponseCode > 0) {
    String response = http.getString();
    Serial.println(response);
  } else {
    String response = http.getString();
    Serial.print("Error sending request: ");
    Serial.println(httpResponseCode);
  }
  http.end();
}

// a mini server that check for new data requests from the cloud
void Listener( void * pvParameters ){
  // The setup code for the listener
  // login to the cloud
  int loginStatus = cloudLogin(hashedUsername, hashedPassword);

  if (loginStatus == 1) {
    Serial.println("Cloud authentication completed for core 0");
  } 
  else {
    Serial.println("Cloud authentication failed for core 0");
  }

  unsigned long listenerPreviousMillis = 0;
  const long controlParameters_updateInterval = 5000; // 5s
  unsigned long controlParUpdatePreviousMillis = 0;
  // const long listeningInterval = 5000;
  // an infinite loop equivalent to the void loop() function on the main core
  for(;;){
    unsigned long currentMillis = millis();

    // update (sync) the control parameters on the server side periodically
    if (currentMillis - controlParUpdatePreviousMillis >= controlParameters_updateInterval) {
      controlParUpdatePreviousMillis = currentMillis;
      updateCloudControlParameters(lightPercentage, fanThreshold, pumpTriggerPercent, lightStartTime, lightStopTime);
    }

    // if (currentMillis - listenerPreviousMillis >= listeningInterval) {
      // listenerPreviousMillis = currentMillis;
      // JSON document for keeping request arguments
      // int *requestArgs = (int*) malloc(10 * sizeof(int));
      const size_t capacity = JSON_OBJECT_SIZE(1) + 256;
      DynamicJsonDocument requestArgs(capacity);
    
      int httpResponseCode = getNewRequest(&requestArgs);

      if (httpResponseCode == -1) {
        Serial.print("Error sending request: ");
        Serial.println(httpResponseCode);
      }
      else {
        // get the request type
        int requestType = requestArgs["type"];
        // the value that go with the request (if applicable)
        int requestValue;
        char requestStringValue[5];

        

        switch (requestType) {
          // No request
          case 0:
            Serial.println("No new request");
            break;

          // Live data
          case 1: {
            Serial.println("Received live data request from cloud server");

            /*************************
            *
            * NOTE!! To be replace with real temp and humid, the random numbers are just for testing
            *
            */
            float randTemp = bme.readTemperature();
            float randAirHumid = bme.readHumidity();
            float randSoilHumid = convertToSoilHumidity(analogRead(SOIL_SENSOR));
            /*
            ****************************/
            
            sendLiveData(randTemp, randAirHumid, randSoilHumid);
            
            break;
          }
          // SET Pump threshold
          case 2: {
            // get the set value
            requestValue = requestArgs["value"];
            Serial.print("Received pump threshold SET request from server, with threshold ");
            Serial.println(requestValue);

            
            // Setting the threshold
            pumpTriggerPercent = requestValue;
            
            break;
          }
          // SET Fan threshold
          case 3: {
            // get the set value
            requestValue = requestArgs["value"];
            Serial.print("Received fan threshold SET request from server, with threshold ");
            Serial.println(requestValue);

            
            // Setting the threshold
            fanThreshold = requestValue;
            
            break;
          }
          // SET Light intensity
          case 4: {
            // get the set value
            requestValue = requestArgs["value"];
            Serial.print("Received light intensity SET request from server, with level ");
            Serial.println(requestValue);

            
            // Setting the threshold
            lightPercentage = requestValue;
            
            break;
          }
          // SET light start time
          case 5: {
            // get the set value
            strncpy(requestStringValue,requestArgs["value"],sizeof(requestStringValue)) ;
            Serial.print("Received light start time SET request from server, with time ");
            Serial.println(requestStringValue);

            
            // Setting the threshold
            lightStartTime = String(requestStringValue);
            
            break;
          }
          // SET light stop time
          case 6: {
            // get the set value
            strncpy(requestStringValue,requestArgs["value"],sizeof(requestStringValue)) ;
            Serial.print("Received light stop time SET request from server, with time ");
            Serial.println(requestStringValue);

            
            // Setting the threshold
            lightStopTime = String(requestStringValue);
            
            break;
          }
          default:
          //
            Serial.print("Received unknown request from cloud server with type: ");
            Serial.println(requestType);
            break;
        }
      }

      // free(requestArgs);
    // }
    // delay to not flood the whole Serial monitor and make it easier to debug
    delay(2000);
  } 
}


// send data with a timestamp of the current time to the server,
// the data is sent to esp-req/sensordata/<timestamp> resource on the cloud server
void sendData(float temp, float airHumid, float soilHumid) {
  // Create a JSON payload with the temperature and humidity values
    StaticJsonDocument<512> jsonPayload;
    jsonPayload["temp"] = temp;
    jsonPayload["air_humid"] = airHumid;
    jsonPayload["soil_humid"] = soilHumid;
    jsonPayload["user_id"] = hashedUsername;
    jsonPayload["password"] = hashedPassword;

    // Serialize the JSON payload to a string
    String payloadString;
    serializeJson(jsonPayload, payloadString);

    String address = BASE_URL + "esp-req/sensordata/";
    char timeStr[20];
    time_t now = time(nullptr);
    struct tm* timeinfo = localtime(&now);
    strftime(timeStr, sizeof(timeStr), "%Y_%m_%d_%H_%M_%S", timeinfo);
    
    String timeStr_String = String(timeStr);
    address = address + timeStr_String;
    HTTPClient http;
    http.begin(address);

    // Set the content type header to JSON
    http.addHeader("Content-Type", "application/json");

    // Send the PUT request with the JSON payload
    int httpResponseCode = http.PUT(payloadString);
    if (httpResponseCode > 0) {
      String response = http.getString();
      Serial.println(response);
    } else {
      String response = http.getString();
      Serial.print("Error sending request: ");
      Serial.println(httpResponseCode);
    }
    http.end();
}

// function for sending live data to /sensordata/live/ resource on cloud server
void sendLiveData(float temp, float airHumid, float soilHumid) {
  // Create a JSON payload with the temperature and humidity values
    StaticJsonDocument<512> jsonPayload;
    jsonPayload["temp"] = temp;
    jsonPayload["air_humid"] = airHumid;
    jsonPayload["soil_humid"] = soilHumid;
    jsonPayload["user_id"] = hashedUsername;
    jsonPayload["password"] = hashedPassword;

    char timeStr[20];
    time_t now = time(nullptr);
    struct tm* timeinfo = localtime(&now);
    strftime(timeStr, sizeof(timeStr), "%Y_%m_%d_%H_%M_%S", timeinfo);
    String timeStr_String = String(timeStr);
    jsonPayload["time"] = timeStr;

    // Serialize the JSON payload to a string
    String payloadString;
    serializeJson(jsonPayload, payloadString);

    // make the address
    String address = BASE_URL + "esp-req/sensordata/live";
    
    HTTPClient http;
    http.begin(address);

    // Set the content type header to JSON
    http.addHeader("Content-Type", "application/json");

    // Send the PUT request with the JSON payload
    int httpResponseCode = http.PUT(payloadString);
    if (httpResponseCode > 0) {
      String response = http.getString();
      Serial.println(response);
    } else {
      String response = http.getString();
      Serial.print("Error sending request: ");
      Serial.println(httpResponseCode);
    }
    http.end();
}

// Function to hash a given string using SHA-256
 String hashString(const char *str) {
  byte hashed_bytes[32];
  
  mbedtls_md_context_t ctx;
  mbedtls_md_type_t md_type = MBEDTLS_MD_SHA256;
  
  const size_t str_length = strlen(str);
  mbedtls_md_init(&ctx);
  mbedtls_md_setup(&ctx, mbedtls_md_info_from_type(md_type), 0);
  mbedtls_md_starts(&ctx);
  mbedtls_md_update(&ctx, (const unsigned char *) str, str_length);
  mbedtls_md_finish(&ctx, hashed_bytes);
  mbedtls_md_free(&ctx);
  
  String hashed_str = "";

  for(int i= 0; i< sizeof(hashed_bytes); i++)
  {
    char temp[3];
    sprintf(temp, "%02x", (int)hashed_bytes[i]);
    
    // Serial.print(str);
    
    // Append the temporary string to the hashed_str result
    hashed_str += temp;
  }

  return hashed_str;
}

// Send a (hashed) pair of username and password to the cloud
// Return the status code: 0 == fail, 1 == succeed
int cloudLogin(String hashedUsername, String hashedPassword) {
  // hash the username and password
  // String hashedUsername = hashString(username);
  // String hashedPassword = hashString(password);

  // Create a JSON payload with the username and password
  // StaticJsonDocument<128> jsonPayload;
  // jsonPayload["user_id"] = hashedUsername;
  // jsonPayload["password"] = hashedPassword;

  // Serialize the JSON payload to a string
  // String payloadString;
  // serializeJson(jsonPayload, payloadString);
  
  // Create the address
  String address = BASE_URL + "auth/login?user_id=" + hashedUsername + "&password=" + hashedPassword;
  HTTPClient http;
  http.begin(address);
  Serial.println("Sending request to " + address);
  // Send HTTP GET request to the cloud to check for incoming request
  int httpResponseCode = http.GET();

  const size_t capacity = JSON_OBJECT_SIZE(1) + 20;
  DynamicJsonDocument requestArgs(capacity);
  if (httpResponseCode > 0) {
      // Extract the session cookie from the response headers
      sessionCookie = http.header("Set-Cookie");

      // Parse the response JSON
      String response = http.getString();
      DeserializationError error = deserializeJson(requestArgs, response);
      if (error) {
          Serial.println("Failed to parse JSON response");
          http.end();
          return -1;
      }
      http.end();
      int loginStatus = requestArgs["status"];
      return loginStatus;
  } else {
      http.end();
      return -1;
  }
}
////////////////////////////////////////////
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
void loop() {
  if(reset) {

    display.clearDisplay();
          display.setTextSize(2);
          display.setTextColor(SSD1306_WHITE);
          display.setCursor(0, 40);
          display.print("Resetting...");
          display.display();
          WiFi.disconnect(false,true);
          delay(2000);
          wm.resetSettings();
          delay(2000);
          ESP.restart();
          
  }
  
  if (screenMode == 0){
    displayTempHumidity();
  } else if (screenMode == 1) {
    displaySoilData();
  } else if (screenMode == 2) {
    displayMenu();
    if(executeMenu){
      //Serial.println(menuPosition);
      switch(menuPosition){
        
        case 0:
          display.clearDisplay();
          display.setTextSize(2);
          display.setTextColor(SSD1306_WHITE);
          display.setCursor(0, 40);
          display.print("Processing\n   ....   ");
          display.display();
          WiFi.disconnect(false,true);
          delay(2000);
          wm.resetSettings();
          delay(2000);
          ESP.restart();
          break;
        case 1:
          Serial.println("MODE 3");
          screenMode = 3;
          r.setUpperBound(100);
          
          break;
        case 2:
          Serial.println("MODE 4");
          screenMode = 4;
          r.setUpperBound(100);
          break;
        case 3:
          screenMode = 5;
          r.setUpperBound(100);
          break;
        case 4:
          screenMode = 0;
          break;

      }
      executeMenu = false;
      menuPosition = 0;
      r.resetPosition();
    }
    
  } else if (screenMode == 3){    
    displayWateringOption();
  } else if (screenMode == 4){    
    displayLightOption();
  } else if (screenMode == 31){
    displayWateringOption2();
  } else if (screenMode = 5){
    displayFanOption();
  }
  
  
  unsigned long currentMillis = millis();

  //adjustLights(); 

  if (currentMillis - lightCheckPreviousMillis >= lightCheckInterval) {
    lightCheckPreviousMillis = currentMillis;

    adjustLights(); 
    
  }
 
  if (currentMillis - pumpCheckPreviousMillis >= pumpCheckInterval) {
    pumpCheckPreviousMillis = currentMillis;

     if (needsWater()) pumpWater();
     if (needsWater()) {
       pumpCheckInterval = 60000;
       watering = true;
     } else  {
       if(offlineMode){

       } else{
         pumpCheckInterval = pumpInterval;
        watering = false;
        char timeStr[20];
        time_t now = time(nullptr);
        struct tm* timeinfo = localtime(&now);
        strftime(timeStr, sizeof(timeStr), "%y/%m/%d %H:%M:%S", timeinfo);
        pumpingTime = String(timeStr);
      }
       
     }
  }
  
  //log and send data
  if (currentMillis - previousMillis >= interval) {
    previousMillis = currentMillis;
    float temp = 0;
    float airHum = 0;
    float soilHum = 0;
    int count = 10;
    for (int i = 0 ; i<count ; ++i){
      temp += bme.readTemperature();
      airHum += bme.readHumidity();
      soilHum += convertToSoilHumidity(analogRead(SOIL_SENSOR));
    }
    temp = temp/(float)count;
    airHum = airHum/(float)count;
    soilHum = soilHum/(float)count;
    logData(temp, airHum, soilHum); //to SDcard
    if(!offlineMode){
      sendData(temp, airHum, soilHum); //to cloud    
    }
    

  }
  checkAirHumidity();
  
}

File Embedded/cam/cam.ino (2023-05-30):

/*********
  Rui Santos
  Complete instructions at https://RandomNerdTutorials.com/esp32-cam-photo-microsd-card-timestamp
  
  Permission is hereby granted, free of charge, to any person obtaining a copy of this software and associated documentation files.
  The above copyright notice and this permission notice shall be included in all copies or substantial portions of the Software.
*********/

#include "esp_camera.h"
#include "FS.h"                // SD Card ESP32
#include "SD_MMC.h"            // SD Card ESP32
#include "soc/soc.h"           // Disable brownout problems
#include "soc/rtc_cntl_reg.h"  // Disable brownout problems
#include "driver/rtc_io.h"
#include <WiFi.h>
#include <WiFiClientSecure.h>
#include "time.h"


// REPLACE WITH YOUR TIMEZONE STRING: https://github.com/nayarsystems/posix_tz_db/blob/master/zones.csv
String myTimezone ="EET-2EEST,M3.5.0/3,M10.5.0/4";

// Constants for photo sending
String hashedUsername = "e3b89e9d33f88e523083d8b4436adcc3726c89e97fd3179a2e102d765d1b16ed";
String serverPath = "/upload-image/" + hashedUsername;
String serverName = "cloud.kovanen.io";
const int serverPort = 443;

WiFiClientSecure client;



// Pin definition for CAMERA_MODEL_AI_THINKER
// Change pin definition if you're using another ESP32 camera module
#define PWDN_GPIO_NUM     32
#define RESET_GPIO_NUM    -1
#define XCLK_GPIO_NUM      0
#define SIOD_GPIO_NUM     26
#define SIOC_GPIO_NUM     27
#define Y9_GPIO_NUM       35
#define Y8_GPIO_NUM       34
#define Y7_GPIO_NUM       39
#define Y6_GPIO_NUM       36
#define Y5_GPIO_NUM       21
#define Y4_GPIO_NUM       19
#define Y3_GPIO_NUM       18
#define Y2_GPIO_NUM        5
#define VSYNC_GPIO_NUM    25
#define HREF_GPIO_NUM     23
#define PCLK_GPIO_NUM     22

// Stores the camera configuration parameters
camera_config_t config;

long currentMillis = 0;
long previousMillis = 0;
//long interval = 1800000;
long interval = 30000;


// Initializes the camera
void configInitCamera(){
  config.ledc_channel = LEDC_CHANNEL_0;
  config.ledc_timer = LEDC_TIMER_0;
  config.pin_d0 = Y2_GPIO_NUM;
  config.pin_d1 = Y3_GPIO_NUM;
  config.pin_d2 = Y4_GPIO_NUM;
  config.pin_d3 = Y5_GPIO_NUM;
  config.pin_d4 = Y6_GPIO_NUM;
  config.pin_d5 = Y7_GPIO_NUM;
  config.pin_d6 = Y8_GPIO_NUM;
  config.pin_d7 = Y9_GPIO_NUM;
  config.pin_xclk = XCLK_GPIO_NUM;
  config.pin_pclk = PCLK_GPIO_NUM;
  config.pin_vsync = VSYNC_GPIO_NUM;
  config.pin_href = HREF_GPIO_NUM;
  config.pin_sscb_sda = SIOD_GPIO_NUM;
  config.pin_sscb_scl = SIOC_GPIO_NUM;
  config.pin_pwdn = PWDN_GPIO_NUM;
  config.pin_reset = RESET_GPIO_NUM;
  config.xclk_freq_hz = 20000000;
  config.pixel_format = PIXFORMAT_JPEG; //YUV422,GRAYSCALE,RGB565,JPEG
  config.grab_mode = CAMERA_GRAB_LATEST;

  // Select lower framesize if the camera doesn't support PSRAM
  if(psramFound()){
    config.frame_size = FRAMESIZE_UXGA; // FRAMESIZE_ + QVGA|CIF|VGA|SVGA|XGA|SXGA|UXGA
    config.jpeg_quality = 10; //0-63 lower number means higher quality
    config.fb_count = 1;
  } else {
    config.frame_size = FRAMESIZE_SVGA;
    config.jpeg_quality = 12;
    config.fb_count = 1;
  }
  
  // Initialize the Camera
  esp_err_t err = esp_camera_init(&config);
  if (err != ESP_OK) {
    Serial.printf("Camera init failed with error 0x%x", err);
    return;
  }
}

// Connect to wifi
void  initWiFi(){
  bool connected = false;
  String ssid = "";
  String pass = "";
  bool psswd = false;
  while(!connected){
    if (Serial.available())
  {
    String input = Serial.readStringUntil('\n');
    input.trim();
    Serial.println("Input:");
    Serial.println(input);
    if (input == "0") {
      
      while(ssid==""){
        if (Serial.available()){
          
          ssid = Serial.readStringUntil('\n');
          ssid.trim();
          Serial.println("Got something:");
          Serial.println(ssid);
        }
      }
      while(!psswd){
        if (Serial.available()){
          pass = Serial.readStringUntil('\n');
          pass.trim();
          Serial.println("Got something:");
          Serial.println(pass);
          psswd = true;          
        }
      }
      WiFi.begin(ssid.c_str(), pass.c_str());
      Serial.println("Connecting Wifi");
      while (WiFi.status() != WL_CONNECTED) {
        Serial.print(".");
        delay(500);
        
      }
      connected = true;
    }
    
  }
  }
  
  
}

// Function to set timezone
void setTimezone(String timezone){
  Serial.printf("  Setting Timezone to %s\n",timezone.c_str());
  setenv("TZ",timezone.c_str(),1);  //  Now adjust the TZ.  Clock settings are adjusted to show the new local time
  tzset();
}

// Connect to NTP server and adjust timezone
void initTime(String timezone){
  struct tm timeinfo;
  Serial.println("Setting up time");
  configTime(0, 0, "pool.ntp.org");    // First connect to NTP server, with 0 TZ offset
  if(!getLocalTime(&timeinfo)){
    Serial.println(" Failed to obtain time");
    return;
  }
  Serial.println("Got the time from NTP");
  // Now we can set the real timezone
  setTimezone(timezone);
}

// Get the picture filename based on the current ime
String getPictureFilename(){
  struct tm timeinfo;
  if(!getLocalTime(&timeinfo)){
    Serial.println("Failed to obtain time");
    return "";
  }
  char timeString[20];
  strftime(timeString, sizeof(timeString), "%Y-%m-%d-%H-%M-%S", &timeinfo);
  Serial.println(timeString);
  String filename = "/picture_" + String(timeString) +".jpg";
  return filename; 
}

// Initialize the micro SD card
void initMicroSDCard(){
  // Start Micro SD card
  Serial.println("Starting SD Card");
  if(!SD_MMC.begin()){
    Serial.println("SD Card Mount Failed");
    return;
  }
  uint8_t cardType = SD_MMC.cardType();
  if(cardType == CARD_NONE){
    Serial.println("No SD Card attached");
    return;
  }
}

// Take photo and save to microSD card
void takeSavePhoto(){
  // Take Picture with Camera
  camera_fb_t * fb = esp_camera_fb_get();
 
  //Uncomment the following lines if you're getting old pictures
  //esp_camera_fb_return(fb); // dispose the buffered image
  //fb = NULL; // reset to capture errors
  //fb = esp_camera_fb_get();
  
  if(!fb) {
    Serial.println("Camera capture failed");
    delay(1000);
    ESP.restart();
  }

  // Path where new picture will be saved in SD Card
  String path = getPictureFilename();
  Serial.printf("Picture file name: %s\n", path.c_str());
  
  // Save picture to microSD card
  fs::FS &fs = SD_MMC; 
  File file = fs.open(path.c_str(),FILE_WRITE);
  if(!file){
    Serial.printf("Failed to open file in writing mode");
  } 
  else {
    file.write(fb->buf, fb->len); // payload (image), payload length
    Serial.printf("Saved: %s\n", path.c_str());
  }
  file.close();
  // send the photo to the server
  sendPhotoFromSDCard(path.c_str());
  esp_camera_fb_return(fb); 
}
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

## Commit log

2023-03-08 Fixed small timestamp bug
    [esp_client.ino]
2023-03-08 Main script for ESP32-S2 to send sensor data and control the lights
2023-03-22 Switched to ESP32-WROOM-32E (pin changes), added soil sensor and pump control
2023-03-23 Added pump power cut off
2023-03-24 Added wifi config and MAPLE login credentials - not working yet
    [main.ino]
2023-03-24 WiFi config fix and added a fan
    [main.ino]
2023-03-24 Code cleanup, fan control fix
    [main.ino]
2023-03-26 Pin changes, added an microSD card breakout with basic code
2023-03-26 Added camera UART connection to ESP for WiFi login.
2023-03-26 Added camera file
2023-03-31 Fixed variable sharing bug between request threads
2023-04-05 Added changelogs.md to keep track of the changes made to the API
2023-04-05 Added basic rotary encoder functionality
2023-04-05 Updated main and cam uart connection
2023-04-09 Fixed camera UART connection, added SDcard data logging
    [cam.ino, main.ino]
2023-04-11 Implement device side authentication
2023-04-11 Change the device side authentication implementation
2023-04-12 Replaced dummy data with live data readings
    [main.ino]
2023-04-13 Added all 3D models and laser cutting files
    [BottomPanel v1.dxf, CableCorner v1.stl, CableCorner v2.stl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]
2023-05-04 Testing pin changes
2023-05-04 Pin number fix
2023-05-05 Fixed the memory error with the HTTPClient object
    [main.ino]
2023-05-05 Implemented delete-all method - For deleting all sensor data associated with a user
2023-05-15 Minor fixes for PCB testing
    [main.ino]
2023-05-15 Apply a tested fix for the HTTP Client that previously causes crashing Original commit from cloud branch f12ecc5
    [main.ino]
2023-05-16 Soil sensor calibration improvement and creating plant check interval
2023-05-16 Added stepper library for later use
2023-05-17 Calibrated sensors, added some automation options, added reboot option
    [main.ino]
2023-05-17 Added PCB KiCad model
    [customPCB.kicad_pcb, customPCB.kicad_sch]
2023-05-19 Added a rotary menu, offline mode and reboot option.
    [main.ino]
2023-05-22 Offline mode and menu bug fixes
    [main.ino]
2023-05-23 Set local timezone, redesigned offline menu, added fan control option, disabled menu for online mode.
    [main.ino]
2023-05-24 Implement a shorthand 'now' to query data from a certain time to the current time
2023-05-26 Fix data sending bug - Increase the JSON payload size to fit the username and password
    [main.ino]
2023-05-26 Adjusted pump timings, uncommented timezone setting, updated camera interval
2023-05-27 Use the filename in the SD card as the filename for the server - Previous name was the default 'esp32-cam'
2023-05-27 Changed pumping variables
2023-05-27 Averageing of sensor readings
2023-05-28 Implemented device side remote control handling
2023-05-28 Make lights turn on before camera
2023-05-30 New files
    [CameraMount v3.stl, CameraMountB v2.stl, ConnectorMount v1.stl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]
